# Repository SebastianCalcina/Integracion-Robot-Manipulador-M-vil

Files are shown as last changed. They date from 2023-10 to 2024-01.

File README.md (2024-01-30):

Indice del Repositorio
CódigoRobotManipulador - Esta carpeta contiene los códigos que se utilizaron para realizar las simulaciones del robot manipulador tanto en MATLAB como utilizando Python
RuedasMecanum - Archivos STL y CAD de las partes del robot móvil que se utilizaron para los análisis y también para la impresión 3D
Lista de Componentes- Lista de cada componente necesario en este proyecto.
Guía Ensamblaje- En este documento se puede observar una guía sobre el desarrollo del proyecto desde la compra de cada componente hasta el ensamblaje.

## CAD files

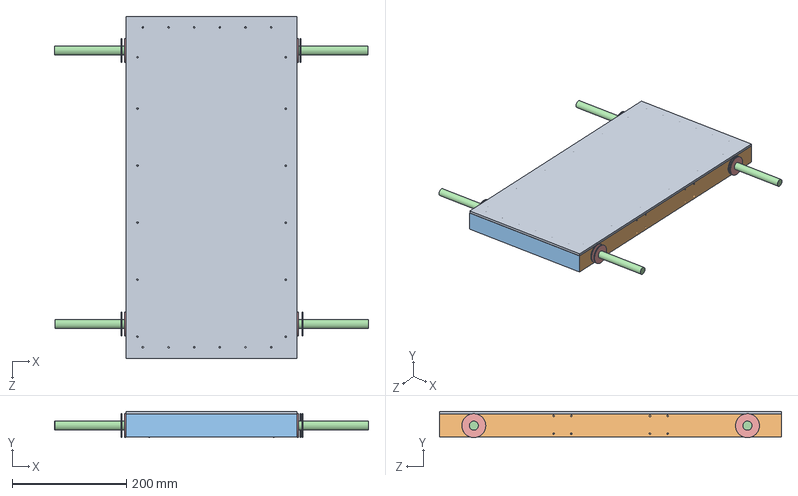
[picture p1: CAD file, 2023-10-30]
Ruedas Mecanum/files/SolidWorks/Movil armado.SLDASM
550.8 x 46.0 x 600.5 mm
Tubo Cuadrado 40x40x1mm angular x 2
tubo cuadrado 40x40x1mm angular 2 x 2
Varilla de 16mm x 2
arandela 16mm x 11
Pieza de madera

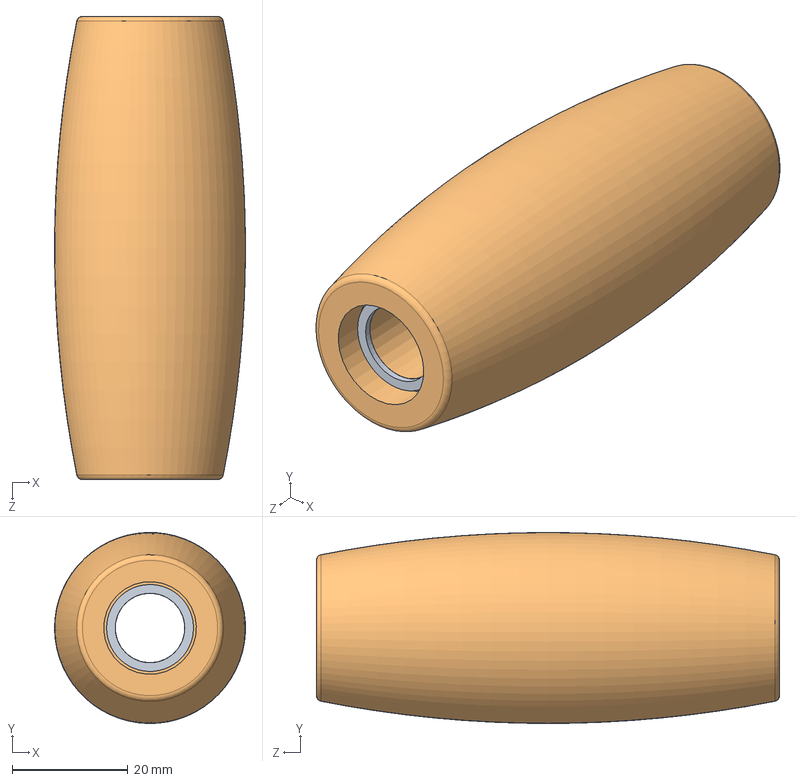
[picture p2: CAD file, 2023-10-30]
Ruedas Mecanum/files/SolidWorks/Ensamblaje Roller.SLDASM
33.0 x 33.0 x 80.0 mm
Arandela Roller x 2
Wheel_print (1)

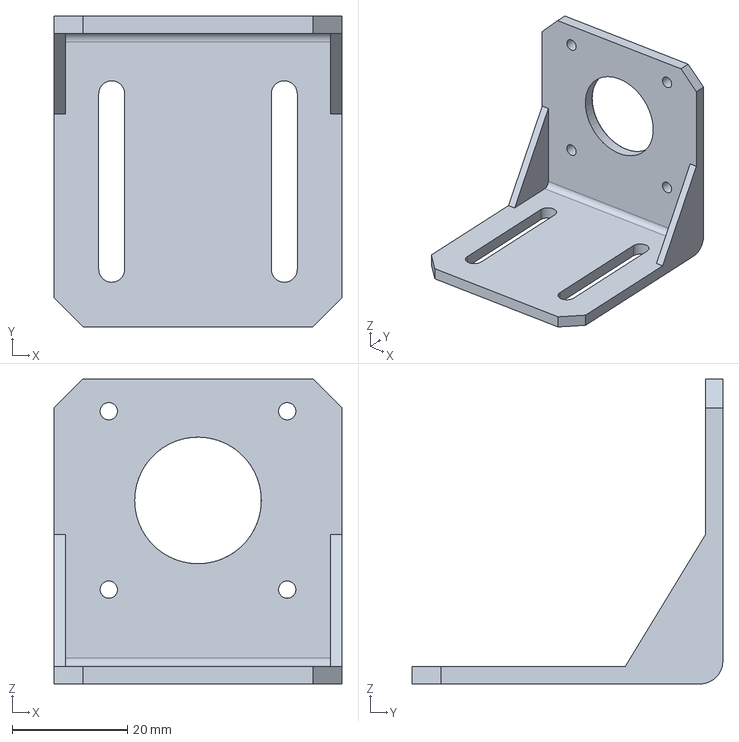
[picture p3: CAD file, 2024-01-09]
Ruedas Mecanum/files/SolidWorks/Soporte90_Nema17.stp
50.0 x 54.0 x 53.0 mm

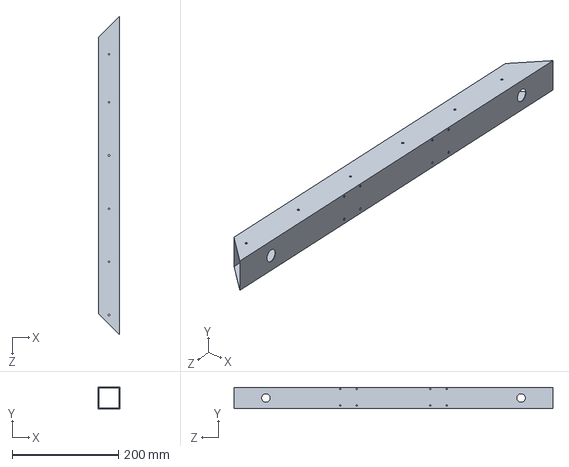
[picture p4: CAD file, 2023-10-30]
Ruedas Mecanum/files/SolidWorks/Tubo Cuadrado 40x40x1mm angular.SLDPRT
40.0 x 40.0 x 600.0 mm

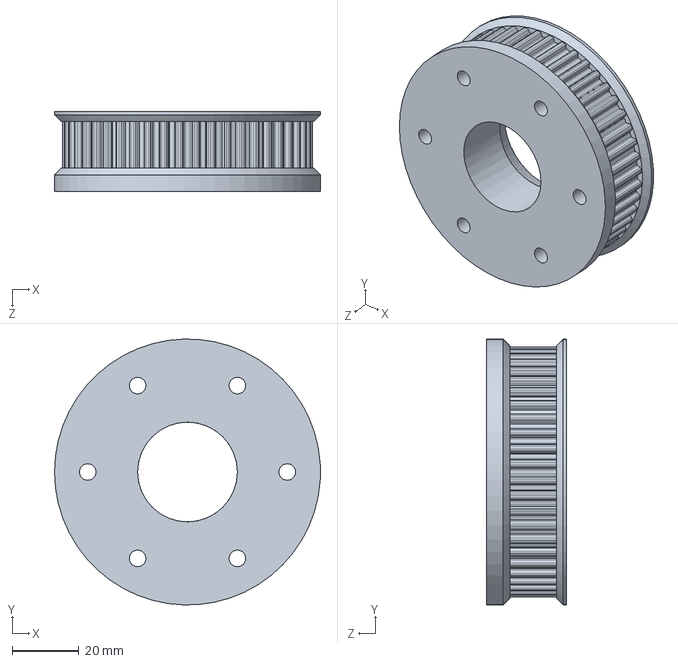
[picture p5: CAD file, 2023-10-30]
Ruedas Mecanum/files/SolidWorks/T5_48z_pulley (1).SLDPRT
80.0 x 80.0 x 24.0 mm

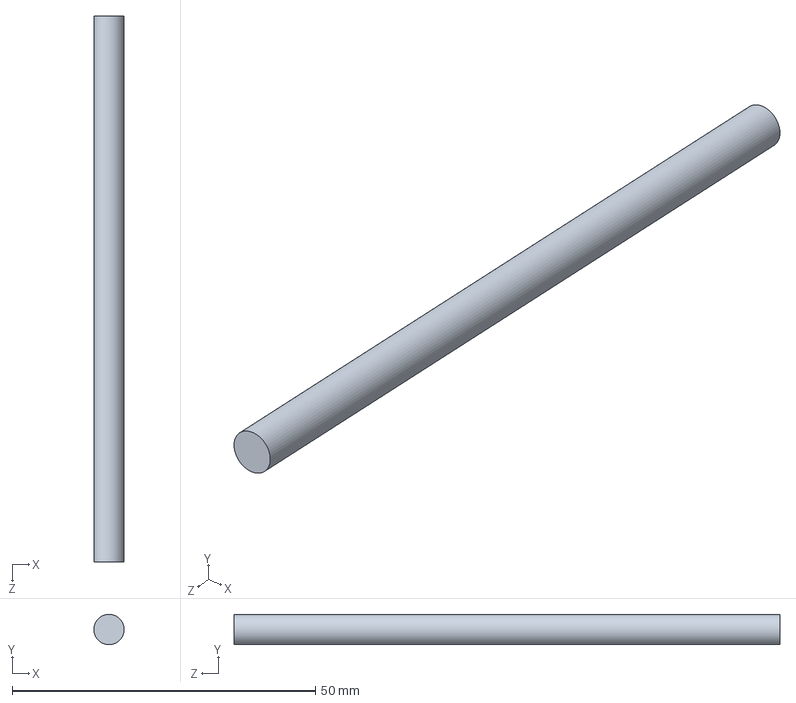
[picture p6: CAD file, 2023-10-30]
Ruedas Mecanum/files/SolidWorks/Varilla Roller 2.SLDPRT
5.00 x 5.00 x 90.0 mm

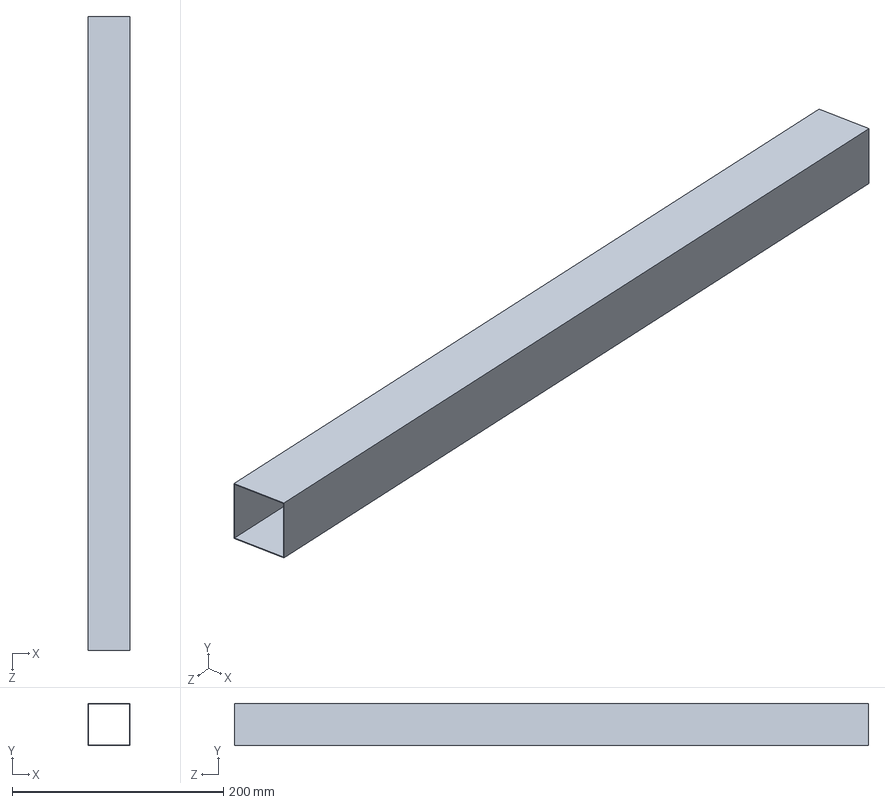
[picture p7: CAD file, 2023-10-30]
Ruedas Mecanum/files/SolidWorks/Tubo Cuadrado 40x40x1mm.SLDPRT
40.0 x 40.0 x 600.0 mm

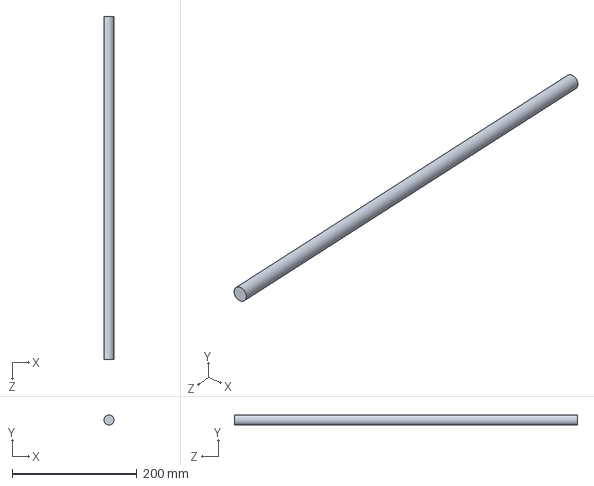
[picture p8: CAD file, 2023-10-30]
Ruedas Mecanum/files/SolidWorks/Varilla de 16mm.SLDPRT
16.0 x 16.0 x 550.0 mm

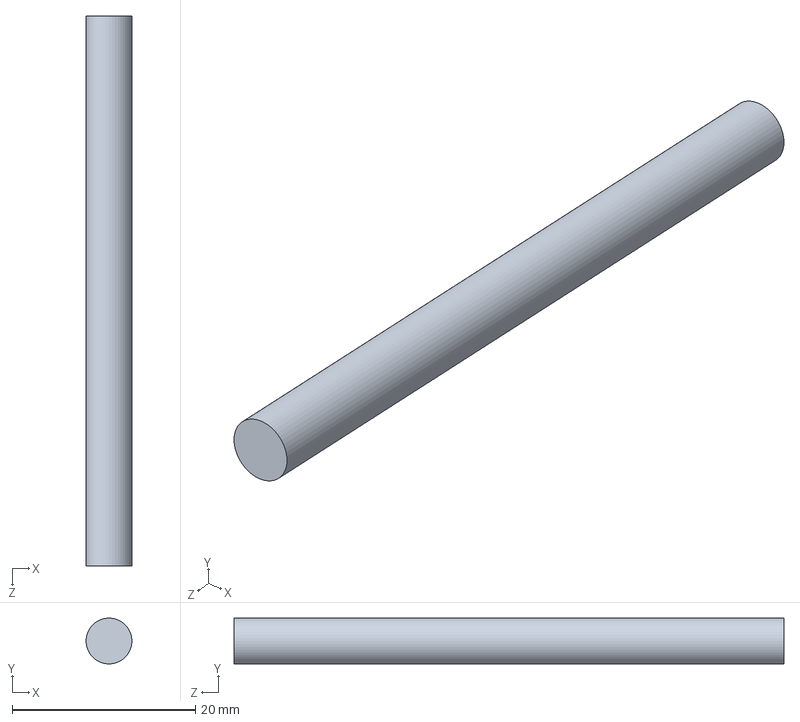
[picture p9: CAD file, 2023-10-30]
Ruedas Mecanum/files/SolidWorks/Varilla Roller 3.SLDPRT
5.00 x 5.00 x 60.0 mm

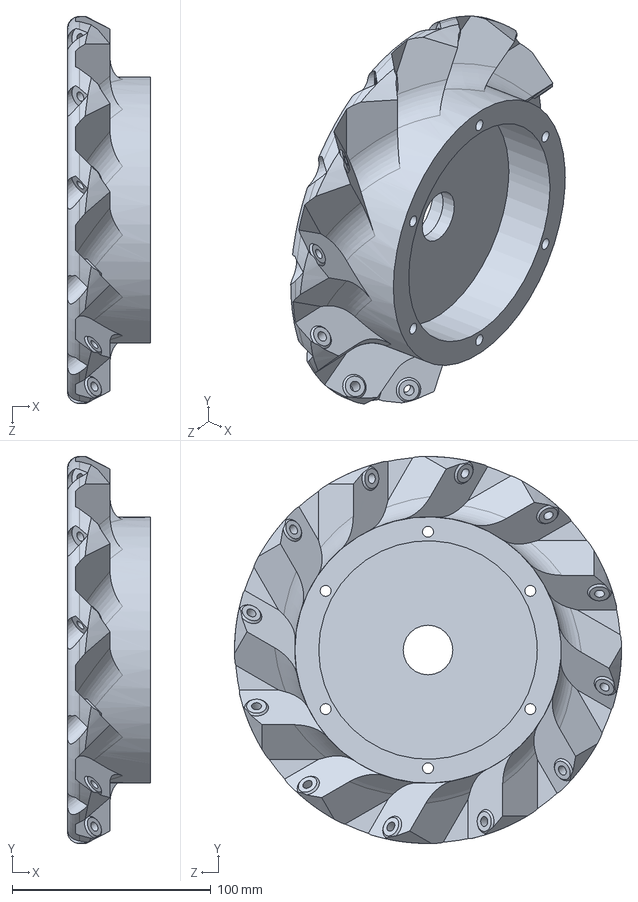
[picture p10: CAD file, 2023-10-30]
Ruedas Mecanum/files/SolidWorks/omniWheel2 (1).SLDPRT
41.8 x 194.8 x 194.8 mm

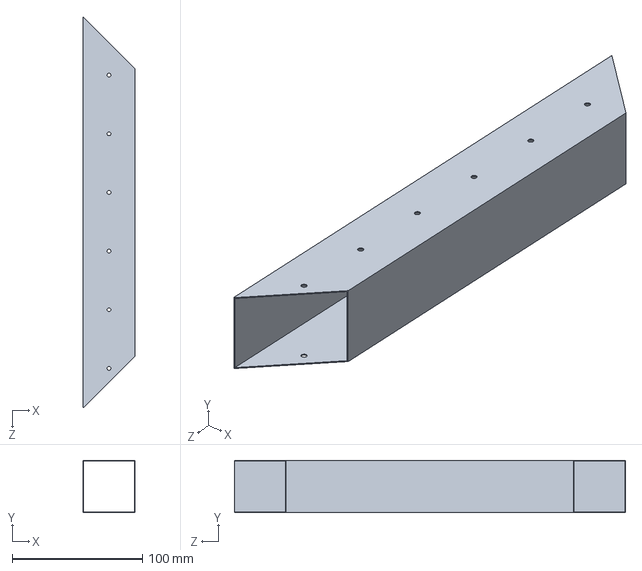
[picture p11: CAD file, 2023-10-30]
Ruedas Mecanum/files/SolidWorks/tubo cuadrado 40x40x1mm angular 2.SLDPRT
40.0 x 40.0 x 300.0 mm

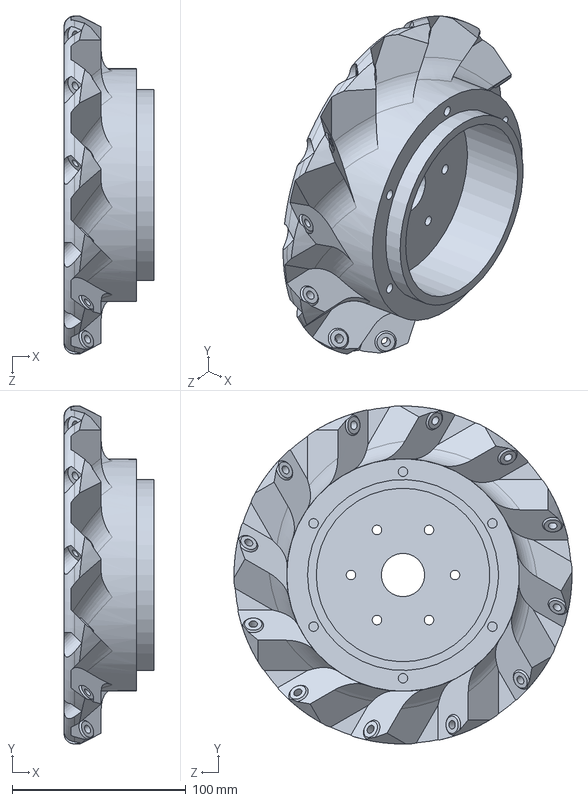
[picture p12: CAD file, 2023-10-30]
Ruedas Mecanum/files/SolidWorks/omniWheel2_B.SLDPRT
51.8 x 194.8 x 194.8 mm

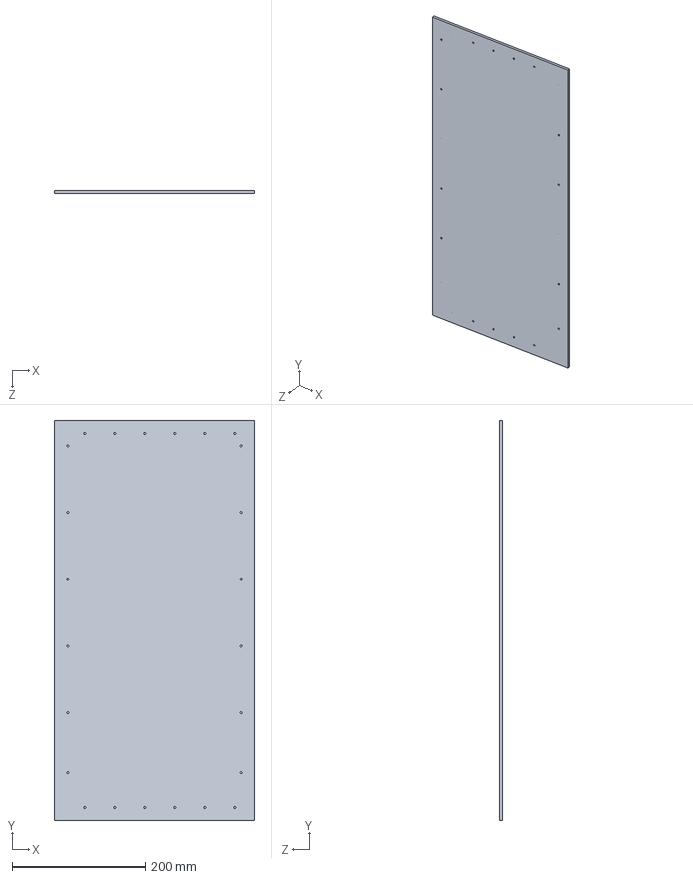
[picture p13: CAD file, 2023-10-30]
Ruedas Mecanum/files/SolidWorks/Pieza de madera.SLDPRT
300.0 x 600.0 x 5.00 mm

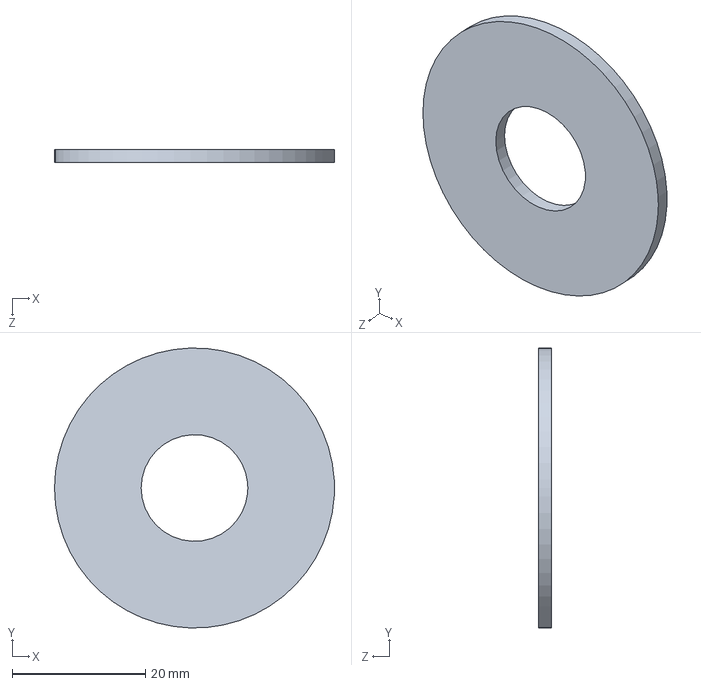
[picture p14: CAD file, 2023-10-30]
Ruedas Mecanum/files/SolidWorks/arandela 16mm.SLDPRT
42.0 x 42.0 x 2.00 mm

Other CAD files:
Ruedas Mecanum/files/SolidWorks/Wheel_print (1).SLDPRT
Ruedas Mecanum/files/SolidWorks/Arandela Roller.SLDPRT

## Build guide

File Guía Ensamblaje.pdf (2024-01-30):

Para el desarrollo del robot manipulador móvil, existen diferentes cosas que hacer, en

el cual de las más importantes están las impresiones y la selección de componentes. A

continuación, se observan los pasos para el desarrollo del proyecto.

Paso 1: Selección de herramientas

En esta sección se detallan las herramientas hardware y software utilizadas en este

proyecto. No es necesario tenerlos todos para comenzar, pero es importante tener en cuenta que

se necesitará a medida que se avance.

- Hardware
− Impresora 3D: Necesaria para imprimir el robot. Área de impresión de 300x300 mm,

suficiente para imprimir cada pieza. Si se posee una impresora con un área de impresión

de 200x200 mm, existen versiones partidas de las piezas más grandes que caben en tu

máquina.

− Estación de soldadura o cautín: Para soldar cables y componentes electrónicos a la

PCB es necesario una estación de soldadura o un cautín simplemente como se observa

en la Figura 1:

Figura 1. Estación de soldadura.

Fuente: (Amazon 2023).

## APENDICE A : GUIA DEL PROYECTO

− Multímetro: Útil a la hora de realizar conexiones electrónicas, probar sensores o

comprobar uniones soldadas. Además de que poder configurar la corriente de los

controladores de motores a la vez.

− Juego de llaves Allen y destornilladores: necesarios para asegurar los tornillos en el

conjunto del robot.

- Software

El desarrollo del robot Thor se ha realizado únicamente con herramientas de código

abierto, por lo que no es necesario gastar dinero en licencias de software.

− FreeCAD: (https://www.freecadweb.org/) Modelador paramétrico 3D. Cada pieza de Thor ha sido modelada utilizando

esta increíble herramienta. Incluso si no hay interés en el diseño de nuevas piezas o

características, se recomienda descargarlo porque hay un archivo FreeCAD que

contiene el ensamblaje del robot que te será de gran ayuda cuando se esté construyendo

el robot. El enlace de descarga es el siguiente: https://www.freecad.org/downloads.php

− KiCAD: (https://www.kicad.org/) Programa de diseño electrónico. Se utiliza para diseñar los PCB de control. Si

se presenta interés en estudiar, modificar o desarrollar electrónica para este o cualquier

otro proyecto. El enlace de descarga de este software es el siguiente:

https://www.kicad.org/download/

− Editor de código: Si es necesario profundizar en las entrañas del software o el firmware

de control, se recomienda utilizar un editor de texto con soporte de código como Atom

o también Visual Studio Code, los cuales se pueden descargar de los siguientes enlaces:

https://github.blog/2022-06-08-sunsetting-atom/

https://code.visualstudio.com/download

− Software | de | Control: | Existe | un | software | llamado | Asgard

https://github.com/AngelLM/Asgard creado especialmente para controlar a Thor.

Caso contrario se puede utilizar el firmware de GRBL al descargar la librería

directamente desde Arduino como se observa en la Figura 2, como se observa en la

siguiente Figura al buscarlo en el administrador de librerías. Dado el caso que no salga

la librería como se observa, se debe descargar la librería grbl desde el siguiente enlace

e incorporarlo dentro de la carpeta de librerías de Arduino: https://github.com/gnea/grbl

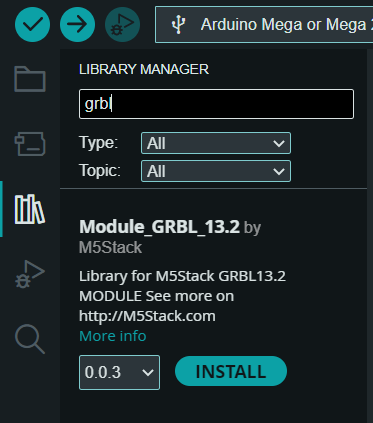
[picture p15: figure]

Figura 2. Descargar librería GRBL.

Fuente: Elaboración propia.

Paso 2: Adquisición de los materiales

Se debe buscar en diferentes tiendas los materiales descritos en el documento como

ser los pernos, tuercas, arandelas, ejes, rodamientos, etc.

Al menos en la ciudad de Santa Cruz, Bolivia existen zonas donde venden los

componentes electrónicos en toda esa zona, y venden todos los materiales de construcción en

otra zona. Los materiales de construcción se encuentran en la Av. Brasil entre 2do y 3er anillo,

como se muestra en la siguiente Figura 3.

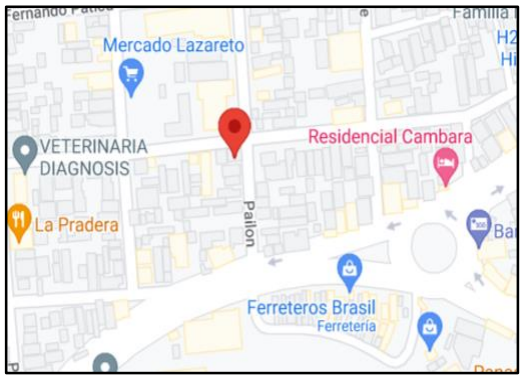
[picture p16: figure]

Figura 3. Ubicación tienda de pernos.

Fuente: Elaboración propia.

En la Tabla 1 y 2 se pueden observar los pernos y tuercas que se deben comprar

necesarios para el proyecto.

Tabla 1. Lista de pernos.

Cantidad | Diámetro [mm] | Largo [mm]
2 | M2 | 4
3 | M2 | 6
2 | M2 | 10
4 | M3 | 6
60 | M3 | 8
4 | M3 | 10
35 | M3 | 12
2 | M3 | 14
37 | M3 | 16
12 | M3 | 20
16 | M3 | 25
8 | M3 | 30
15 | M3 | 40
8 | M3 | 46
4 | M4 | 20
1 | M5 | 16

Fuente: (Larrañaga 2015).

Tabla 2. Lista de tuercas.

Cantidad | Tamaño [mm]
4 | M2
155 | M3
4 | M4
1 | M5

Fuente: (Larrañaga 2015).

Los componentes electrónicos se hallaron en el centro de la ciudad, específicamente

en la calle Charcas como se puede observar en la Figura 4, esta zona es conocida debido a que

existen gran cantidad de electrónicas en esta zona, pero para el proyecto la mayor parte de

componentes se encontraron en la tienda Sawers, Ardunel y EPY, los cuales son los 3

distribuidores más grandes de componentes electrónicos.

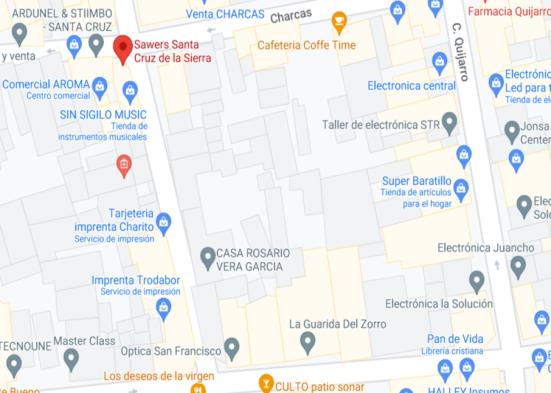
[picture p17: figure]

Figura 4. Ubicación Sawers.

Fuente: Elaboración propia.

En cualquiera de estas zonas venden herramientas, las cuales son necesarias

posteriormente para la fabricación del robot manipulador móvil. Además de que venden los

materiales necesarios para la fabricación de la placa electrónica.

Posteriormente, se muestra la tienda donde se adquirió los filamentos para la impresión

de las piezas, su ubicación se muestra en la Figura 5, cabe aclarar que en la zona de electrónicas

también se puede encontrar filamentos para impresoras 3D, pero, a un precio más alto, en este

caso se desea que sea lo más económico posible, por lo tanto, se compra los filamentos en la

tienda llamada Savin.

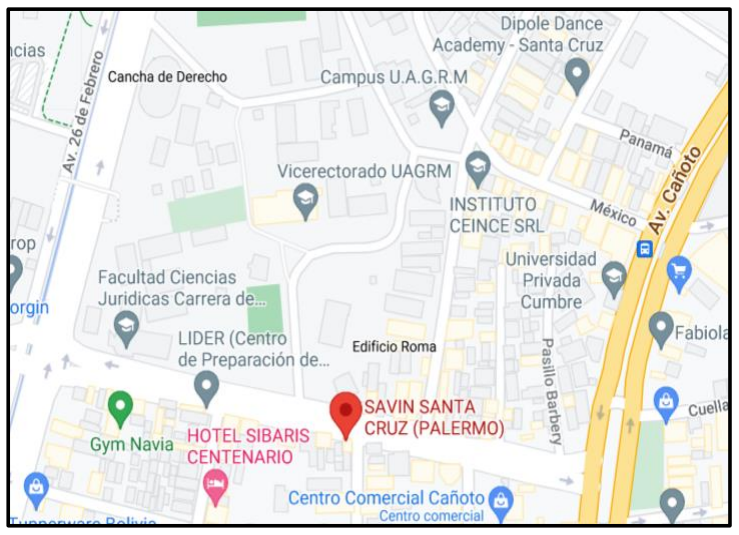
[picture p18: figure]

Figura 5. Ubicación Savin.

Fuente: Elaboración propia.

Se recomienda verificar el stock de los componentes primero mediante sus sitios web,

los cuales se adjuntan a continuación, caso contrario no exista stock en esta sucursal, se puede

solicitar desde otro departamento. En el caso de Sawers la solicitud no tiene costo y envían el

componente sin costo de envío, en el caso de Ardunel cobran el envío desde otro departamento

y uno debe recogerlo desde la Terminal Bimodal. Para el caso de Savin, existe la posibilidad de

recogerlo desde la Terminal Bimodal o desde su sucursal en el departamento de Santa Cruz,

pero tienen un costo variable.

Savin: https://www.savin.com.bo/savin3d/index.html

Sawers: https://tienda.sawers.com.bo/

Ardunel: https://tienda.sawers.com.bo/

Por último, en el caso de este proyecto, se tuvo dificultad encontrando ciertos

componentes, los cuales a continuación se muestran cuáles fueron los componentes difíciles de

encontrar, los cuales, si se encuentra una mejor solución, se recomienda aplicarla. El primer

componente son los pernos M2, en las tiendas mayoristas de pernos tampoco traen este tamaño

de perno debido a que no son pernos comerciales, son más que todo utilizados por empresas en

el ensamblaje de computadoras.

En este caso se encontró una caja en la electrónica Ardunel en la cual se encontraban

diferentes pernos de distintos tamaños entre ellos M2, M2.5, M3. Por lo tanto, se compra este

kit de pernos para poder conseguir estos pernos que sirven para el servomotor. El cual se

observa en la Figura 6.

Figura 6. Kit de pernos y tuercas.

Fuente: Elaboración propia.

El siguiente componente que no se encuentra con facilidad son los pernos M3 de 40mm

y 46mm de largo, los cuales se buscaron en diferentes tiendas pero no hubo éxito, por lo tanto,

se decidió buscar en tiendas de electronica de otros departamentos, en el cual en el siguiente

enlace se encontraron estos pernos, por lo tanto, de esta manera se solucionó la falta de stock

de este componente. Enlace: http://dro-bots.com/

Por último, el otro componente que se dificulta obtener es el motor paso a paso

17HS13-0404S-PG5, el cual no se encuentra en ninguna tienda de Bolivia, para su compra

existen dos opciones:

- Solicitar a una tienda como Sawers el pedido del motor paso a paso: En este

procedimiento existen ventajas como desventajas. La principal ventaja es que solamente cobran el costo del componente más un 5% del monto total. La desventaja es que este

procedimiento tarda alrededor de 2 a 3 meses, por lo cual, en este caso se decidió optar

por otra opción.

- Realizar la compra personalmente mediante la página oficial de motores paso a paso, en

la cual, al ser una persona que no importa componentes con frecuencia ni que tiene

conocimientos sobre ello, el precio fue alto considerando el envio y los impuestos de

los componentes. La ventaja es que solamente tarda alrededor de 15 días, por lo tanto,

se recomienda realizar el pedido mediante Sawers para evitar un costo alto. El enlace

de la página para comprar los motores paso a paso es el siguiente:

https://www.omc-stepperonline.com/nema-17-stepper-motor-bipolar-l-33mm-w-gear-

ratio-5-1-planetary-gearbox-17hs13-0404s-pg5?tracking=5c5b1e7294397 (https://www.omc-stepperonline.com/nema-17-stepper-motor-bipolar-l-33mm-w-gear-ratio-5-1-planetary-gearbox-17hs13-0404s-pg5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)

Paso 3: Impresión de los archivos CAD

Cada impresora 3D es diferente y ninguna funciona de la misma manera, sin embargo,

aquí hay algunas recomendaciones generales que pueden resultar útiles:

− Piezas Grandes: Debido a la resistencia mecánica, sería mejor imprimir las piezas

grandes (las de Articulación 2) en una sola pieza. Si no caben en la impresora, hay

versiones divididas se encuentran en la carpeta "Mods".

− Materiales: Casi todas las piezas se pueden imprimir en PLA (barato y fácil de

imprimir).

− Optodiscos: Las piezas Art1Bot, Art23Optodisk, Art4Optodisk se utilizan para bloquear

la luz de un sensor óptico en todas las posiciones excepto donde se encuentra la

ranura. Como las paredes del disco son delgadas y permite el paso de la luz, se

recomienda cubrir la superficie de estas piezas con pintura base o esmalte de uñas,

teniendo cuidado de no tapar la ranura.

− Configuración de impresión: Como las piezas son bastante grandes, se recomienda

utilizar alturas de capa gruesas, como 0,3 mm, para reducir el tiempo de impresión. En

general, 3-4 paredes deberían ser suficientes con un 20% de relleno.

− Soportes: Algunas partes de las piezas han sido diseñadas a 45 grados para evitar la

necesidad de soportes durante la impresión. Sin embargo, algunas piezas necesitan

soportes para imprimir bien, por lo que sería una buena idea habilitar los soportes para

cada ángulo superior a 50 grados en todas las impresiones.

Para iniciar la impresión de los archivos se necesita una impresora 3D con un área de

impresión de 300x300x220mm de área de impresión y boquilla de 0,4mm y adquirir la cantidad

de PLA contenido en el documento principal. Los archivos CAD se encuentra en la descripción

del | anexo | A | y | también | se | puede | descargar | en | el | siguiente | enlace:

https://github.com/AngelLM/Thor.

Se recomienda imprimir las piezas a una velocidad de 50 m/s para así obtener

resultados precisos en agujeros, engranajes, soportes, etc. Para la impresión de todos los

archivos, se utiliza el software de impresión llamado “CuraSlicer”. Este software es de acceso

gratuito, por lo tanto, no existe problema en su adquisición.

En la Figura 7 se observa la configuración que se debe realizar para la impresión de

las piezas y así tener un buen acabado y tener los menores errores posibles en su impresión. En

esta Figura se observa la configuración de la sección de calidad, en el cual se modifica la altura

de capa, la altura de capa inicial y el ancho de línea, estos parámetros se cambian debido a que

por defecto vienen en unos valores diferentes, pero con estos parámetros se puede ahorrar un

poco de tiempo en la impresión sin afectar en la calidad de la pieza.

Figura 7. Sección de Calidad en CuraSlicer.

Fuente: Elaboración propia.

La siguiente configuración que se debe cambiar son la cantidad de capas superiores e

inferiores, las cuales se pueden aumentar o disminuir, pero es importante mantenerlas en 3 para

así tener un buen acabado y a la vez que no tome mucho tiempo extra de impresión como se

observa en la Figura 8.

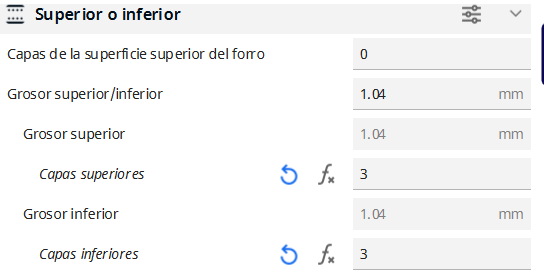
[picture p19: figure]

Figura 8. Sección de Superior o inferior en CuraSlicer.

Fuente: Elaboración propia.

En la Figura 9 se observa la sección de relleno, la cual se coloca como densidad de

relleno de 30% y se utiliza el patrón de relleno cúbico, este relleno cúbico tiene la característica

de que es un relleno que hace que la estructura de la pieza sea estable y también a un tiempo

moderado, existen otros rellenos los cuales tardan más tiempo y tienen mayor durabilidad, pero

con las características que proporciona este relleno es suficiente.

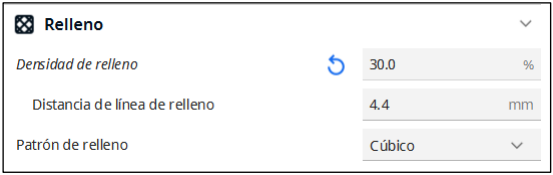
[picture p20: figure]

Figura 9. Sección de Relleno en CuraSlicer.

Fuente: Elaboración propia.

Un consejo útil es emplear laca para el cabello en piezas grandes. Esto se debe a que,

en ausencia de una impresora 3D con ambiente cerrado, cualquier corriente de aire a una

temperatura distinta de la que se encuentra la cama de impresión puede dar lugar al fenómeno

conocido como "warping". El warping se refiere al levantamiento de las esquinas de la pieza en

proceso de impresión, y es un error bastante común en la impresión 3D.

Otro consejo previamente a realizar la impresión es realizar la calibración de la

impresora 3D, principalmente las excéntricas, los pasos/mm de los motores paso a paso y por

último, los resortes que nivelan las cuatros esquinas de la cama de la impresora 3D.

A continuación, se presentan los pasos para verificar el estado de las excéntricas:

1. Asegúrate de que las excéntricas pueden moverse fácilmente al ejercer una ligera

presión con el dedo.

2. Verifica que, si las excéntricas se mueven con facilidad, pero no provocan el giro

del extrusor o la cama, esto indica que están demasiado flojas.

3. Si las excéntricas no se mueven y presentan signos de desgaste, es necesario

aflojarlas.

Realizar estos pasos se garantiza el correcto funcionamiento de las excéntricas en tu

impresora 3D, las cuales se muestran a continuación.

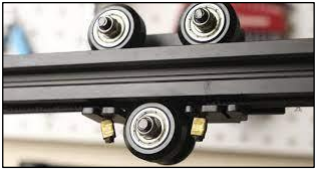
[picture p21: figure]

Figura 10. Excéntricas en una impresora 3D.

Fuente: Elaboración propia.

Los resortes de la cama desempeñan un papel crucial al nivelar la superficie de

impresión en una impresora 3D. Esto es de suma importancia para evitar daños en la cama y

garantizar una impresión precisa. Aunque muchas impresoras 3D modernas están equipadas

con sistemas de nivelación automática que utilizan sensores táctiles, se aconseja realizar un

nivelado manual utilizando una hoja de papel A4, como se ilustra en la Figura 11, esto se debe

realizar en cada una de las cuatro esquinas de la cama y por último en el centro, para así

modificar el valor de z offset.

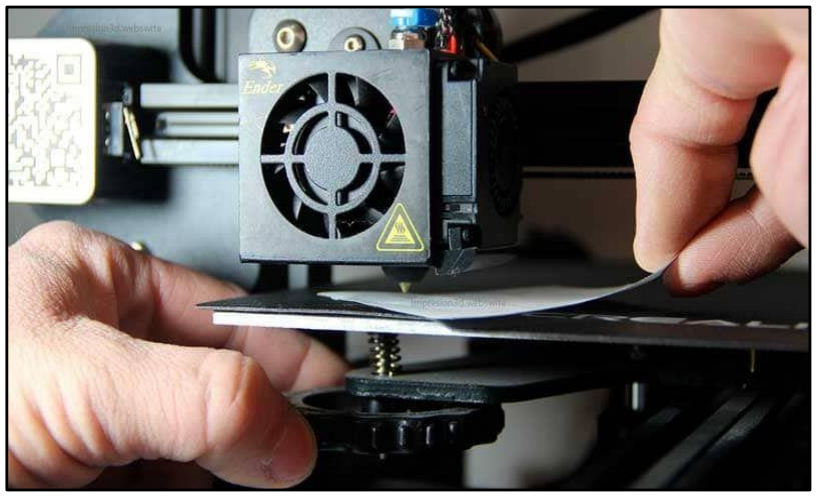
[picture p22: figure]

Figura 11. Calibración de una impresora 3D.

Fuente: Elaboración propia.

Por último, en la Tabla 3 se pueden observar las piezas a imprimir con su respectivo

tiempo de impresión.

Tabla 3. Partes del Brazo manipulador de 6 grados de libertad “Thor”.

Pieza | Tiempo de impresión | Consumo de filamento
Pieza 1: BaseBot | 19 horas | 261 gramos
Pieza 2: BaseTop | 7 horas y 26 minutos | 129 gramos
Pieza 3: BaseBearingFix | 2 horas y 5 minutos | 35 gramos
Pieza 4: BaseBoxBody | 23 horas y 9 minutos | 289 gramos
Pieza 5: BaseBoxCover | 5 horas y 9 minutos | 93 gramos
Pieza 6: Art1Body | 1 día y 7 horas. | 421 gramos
Pieza 7: Art1Bot | 5 horas y 42 minutos. | 75 gramos
Pieza 8: Art1Top | 8 horas y 22 minutos | 132 gramos
Pieza 9 y 10: Art1FanHolder | 30 minutos | 4 gramos
Pieza 11: Art1GearMotor | 36 minutos | 7 gramos
Pieza 12: Art1OptoFix | 20 minutos | 4 gramos
Pieza 13: Art2BodyA | 12 horas y 13 minutos | 168 gramos
Pieza 14: Art2BodyACover1 | 2 horas | 33 gramos
Pieza 15: Art2BodyACover2 | 2 horas | 31 gramos
Pieza 16: Art2BodyAWindow | 2 horas | 27 gramos
Pieza 17: Art2BodyB | 13 horas y 26 minutos | 198 gramos
Pieza 18: Art2BodyBCover | 3 horas y 53 minutos | 66 gramos
Pieza 19: Art2BodyUnion | 4 horas y 40 minutos | 60 gramos
Pieza 20: Art2GearMotor | 1 hora y 22 minutos | 14 gramos
Pieza 21 y 22: Art2SideCover | 6 horas y 49 minutos | 103 gramos
Pieza 23: Art3Body | 1 dia y 1 hora | 341 gramos
Pieza 24: Art3Pulley | 3 horas y 3 minutos | 37 gramos
Pieza 25: Art3TensionerBody | 16 minutos | 2 gramos
Pieza 26: Art3TensionerPulley | 16 minutos | 3 gramos
Pieza 27: Art4Body | 23 horas y 30 minutos | 307 gramos
Pieza 28: Art4BearingFix | 10 minutos | 2 gramos
Pieza 29: Art4BearingPlug | 4 minutos | 1 gramo
Pieza 30: Art4BearingRing | 2 horas | 24 gramos
Pieza 31: Art4BodyBot | 2 horas y 18 minutos | 32 gramos
Pieza 32: Art4BodyFan | 3 horas | 35 gramos
Pieza 33: Art4MotorFix | 22 minutos | 4 gramos
Pieza 34: Art4MotorGear | 35 minutos | 7 gramos
Pieza 35: Art4OptoDisk | 34 minutos | 8 gramos
Pieza 36: Art4TransmissionColumn | 4 horas y 35 minutos | 59 gramos
Pieza 37: Art23OptoDisk | 24 minutos | 4 gramos
Pieza 38: Art56GearPlate | 5 horas y 12 minutos | 67 gramos
Pieza 39: Art56MotorCoverRing | 2 horas y 24 minutos | 34 gramos
Pieza 40: Art56MotorHolderA | 35 minutos | 6 gramos
Pieza 41: Art56MotorHolderB | 34 minutos | 6 gramos
Pieza 42: Art56SmallGear | 1 hora y 39 minutos | 15 gramos
Pieza 43: CommonBearingFix | 23 minutos | 4 gramos

Pieza 44: CommonBearingFixThrough | 23 minutos | 3 gramos
Pieza 45: GripperActiveArm | 18 minutos | 9 gramos
Pieza 46: GripperArm | 9 minutos | 2 gramos
Pieza 47: GripperBot | 2 horas y 17 minutos | 25 gramos
Pieza 48: GripperFinger | 1 hora y 30 minutos | 20 gramos
Pieza 49: GripperPassiveArm | 15 minutos | 3 gramos
Pieza 50: GripperTop | 1 hora y 9 minutos | 16 gramos

Fuente: Elaboración propia.

Paso 3: Elaboración de la placa PCB

Dentro de la fabricación de la PCB, existen diferentes pasos a realizar, el cual el

primero es determinar los requerimientos y los componentes que conforman esta placa

electrónica, lo cual se realiza en el documento, pero para realizar esto se necesita un software

de electrónica, en este caso se utiliza el software llamado Proteus, el cual permite realizar

diseños esquemáticos y también realizar diseños para la fabricación de placas electrónicas.

En el documento se muestra un diseño en 3D de la placa electrónica, el cual se realiza

mediante la descarga de los archivos “STEP” de los componentes electrónicos. Estos archivos

se encuentran normalmente en la página snapEDA, la cual contiene muchos archivos CAD de

los componentes electrónicos mayormente utilizados.

Estos archivos se deben colocar en la carpeta que se cree el archivo del proyecto, para

que así automáticamente se coloquen, caso contrario se pueden exportar estos archivos uno por

uno al programa, pero esto es más tardío.

En algunos casos se realiza primero el diseño esquemático, pero en este caso se realiza

directamente el diseño en la sección PCB del software, debido a que cuando se realiza el diseño

esquemático primero y se lo trata de exportar, las conexiones que realiza el software

automáticamente suelen no estar correctamente hechas, por lo tanto, para ahorrar tiempo se

procura realizarlo directamente.

El proceso de diseñar y fabricar una placa de circuito impreso (PCB) implica varios

pasos. A continuación, se detallan los pasos para llevar a cabo este proceso:

### 1. Diseño del Esquemático:

Definir la funcionalidad del circuito y crear un esquema eléctrico en software de diseño

como KiCad, Eagle, Altium, Proteus, etc.

En este caso se utiliza Proteus para realizar el diseño electrónico, por lo tanto, una vez

se tiene eso definido, se procura a definir la funcionalidad del circuito.

En el proyecto Thor, se parte de un circuito base que incluye motores paso a paso como

componentes principales encargados de controlar el movimiento y la posición del brazo

manipulador. Para determinar qué motores son adecuados para el robot móvil, cuyo objetivo es

conocer su posición en los ejes x, y, se opta por utilizar motores paso a paso. Estos motores

permiten obtener información precisa sobre la posición y velocidad del robot móvil a través de

los pasos dados.

Una vez definidos los motores a utilizar, se identifica la necesidad de contar con

controladores específicos para los motores paso a paso. Con el propósito de lograr una alta

precisión en el robot manipulador, se elige el controlador DRV8825. Por otro lado, para el robot

móvil, donde no se requiere la misma precisión, se emplea el controlador A4988. Esta selección

de controladores se basa en la necesidad de adaptar la precisión de control a las características

particulares de cada componente del proyecto.

El uso de finales de carrera no se cambia ni tampoco el final de carrera a utilizar, por

lo tanto, ese componente se mantiene de la misma manera, así como los ventiladores y el

servomotor MG995.

Por último, se considera la posibilidad de colocar la computadora encima del robot

móvil para realizar el control del robot móvil, pero se la descarta debido a distintos factores:

- Seguridad: El colocar una computadora encima del robot móvil puede salir mal

si es que no se tiene cuidado en las velocidades utilizadas o en los movimientos

del brazo manipulador.

- Espacio: No hay el suficiente espacio para colocar una computadora encima

del robot móvil y no es la opción más eficiente.

Debido a estas consideraciones se decide implementar un módulo Bluetooth, para así

poder mandar los comandos a distancia, además de que no se pretende que se emplee en un área

grande, por lo tanto, con el alcance del Bluetooth es más que suficiente.

### 2. Diseño de la PCB

- Abrir un nuevo proyecto de PCB en Proteus.
- Establecer una medida de la placa según el espacio que se pueda utilizar para

así tener una mejor distribución de los componentes.

- Coloca los componentes en la PCB y enruta las conexiones entre ellos.
- Revisar que no existan rutas en 90 grados para así evitar cortos circuitos.
- Revisar varias veces si todas las GND están conectadas entre ellas.
- Asegurarse de que el diseño sea eficiente y tenga rutas de señal cortas para

minimizar interferencias electromagnéticas.

- Considera la disposición de componentes para facilitar el ensamblaje.}
- Realiza comprobaciones de reglas de diseño para asegurarte de que no haya

errores, como cortocircuitos o violaciones de restricciones.

### 3. Generación de Archivos:

Exportar el archivo PDF desde Proteus. Estos archivos describen la capa de cobre,

capas de máscara, capas de soldadura, taladros, etc. La cual es importante para realizar la

fabricación PCB.

Para la fabricación PCB existen dos opciones:

- Enviar el diseño a que sea realizado mediante CNC, lo cual es una manera más

sencilla de realizar la placa PCB, pero tiene un costo mayor.

- Realizarlo en el aula o en casa, para así tener aprender distintos conceptos de

la electrónica y habilidades de soldadura.

Dado el caso que se elija realizar la placa por cuenta propia, se debe comprar los

componentes necesarios, los cuales se adjuntan a continuación en la Tabla 4:

Tabla 4. Lista de componentes para la placa.

Componente | Cantidad
Resistencia 220 | 5
Resistencia 1k | 5
Regulador de voltaje | 1
Fusible GF1100 | 1
Controlador A4988 | 4
Controlador DRV8825 | 7
Arduino Mega 2560 | 1
Espadines Hembra | 20
Espadines Macho | 20
Bluetooth HC-05 | 1
Placa de cobre 15x15cm | 1
Metro de estaño | 4
Cautín | 1
Pasta de soldar | 1
Esponja de acero | 1
Estilete | 1
Litro de ácido férrico | 1

Fuente: Elaboración propia.

Una vez se tienen los componentes necesarios, se procede a realizar la placa PCB, el

primer paso es tener la hoja impresa en papel termotransferible como se observa a continuación

en la Figura 12:

Figura 12. Hoja impresa en papel termotransferible.

Fuente: Elaboración propia.

Una vez se corta los papeles a la medida de la placa, se la debe colocar justo a la

medida sin que sobresalga, esto es importante ya que puede arruinar el diseño desde un

principio. Posterior a esto, se le debe pasar con una esponja de acero inoxidable a la plancha

para sacar cualquier impureza y luego con una plancha caliente para que el contenido de la hoja

pase a la placa de cobre. Este paso se puede observar en la Figura 13 mostrada a continuación.

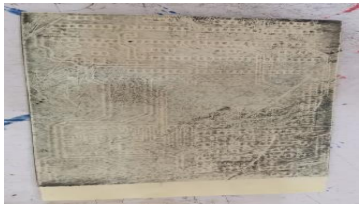
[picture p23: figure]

Figura 13. Hoja planchada en la placa de cobre.

Fuente: Elaboración propia.

Este paso se realiza tanto para la cara superior como para la cara inferior, por lo tanto,

una vez se realiza esto, se lo debe retirar para que así quede como se ilustra en la Figura 14:

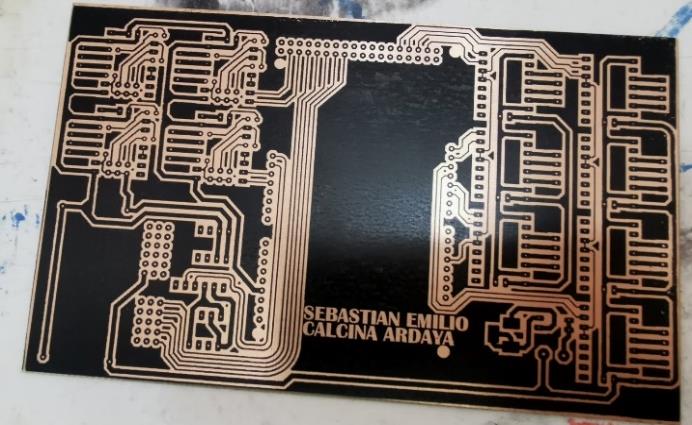
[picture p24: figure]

Figura 14. Diseño PCB transferido a la placa de cobre.

Fuente: Elaboración propia.

Una vez que se tiene el circuito planchado en la placa, se debe asegurar que el diseño

no se salga utilizando ácido férrico, en el cual se diluye en un litro de agua un poco del ácido

férrico para así realizar el grabado utilizando esta mezcla como se observa en la Figura 15.

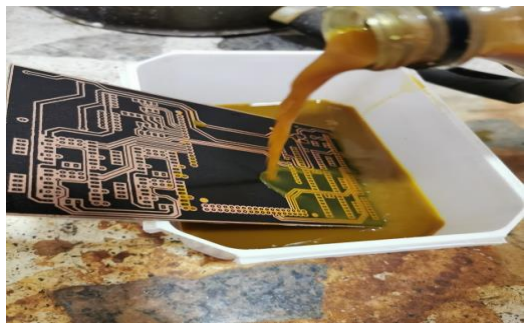
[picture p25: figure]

Figura 15. Grabado del diseño PCB.

Fuente: Elaboración propia.

Este paso se debe repetir una y otra vez hasta que se vea que la placa tiene un color

resplandeciente y posterior a ello, se le debe pasar nuevamente con una esponja de acero para

eliminar los espacios negros que existen en la placa PCB, de manera que queda como se observa

en la Figura 16.

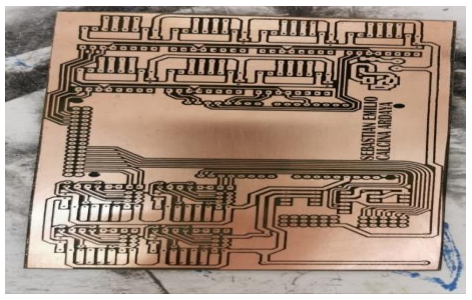
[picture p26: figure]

Figura 16. Grabado del diseño PCB.

Fuente: Elaboración propia.

Como se observa en la anterior Figura quedan los residuos alrededor, por lo tanto, se

debe tener un espacio de trabajo que se pueda ensuciar, o utilizar una manta por debajo para así

no ensuciar el espacio de trabajo.

Posterior a ello, se deben realizar los agujeros para colocar los espadines necesarios

para conectar los componentes posteriormente, en la Figura 17 se observa cómo están los

agujeros realizados, los cuales tienen distintas medidas, pero la mayor parte son de 0.1 mm y el

agujero más grande es de 3mm, los cuales son para poder asegurar la placa electrónica en la

caja de componentes.

Figura 17. Agujeros en la placa PCB.

Fuente: Elaboración propia.

Una vez se realizan los agujeros, el siguiente paso es realizar la soldadura de los

componentes como se observa a continuación en la Figura 18, en este paso se debe realizar con

mucha paciencia las soldaduras y asegurar de que no se conecten entre pines debido a que puede

causar un corto circuito cuando se realice alguna conexión.

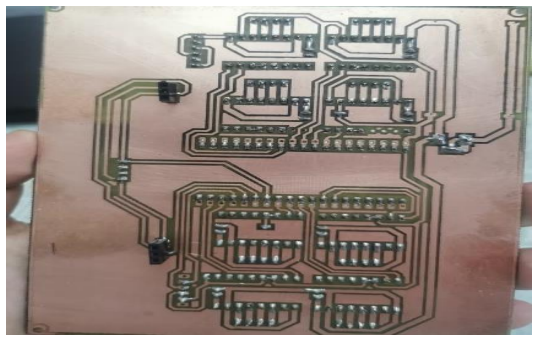
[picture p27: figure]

Figura 18. Soldadura en la placa PCB.

Fuente: Elaboración propia.

Una vez se terminan las soldaduras, se observa que la placa queda de la siguiente

manera que se observa en la Figura 19, la cual ya está lista para realizarse las pruebas

correspondientes de cada uno de los componentes, pero es recomendable verificar la

continuidad utilizando un tester.

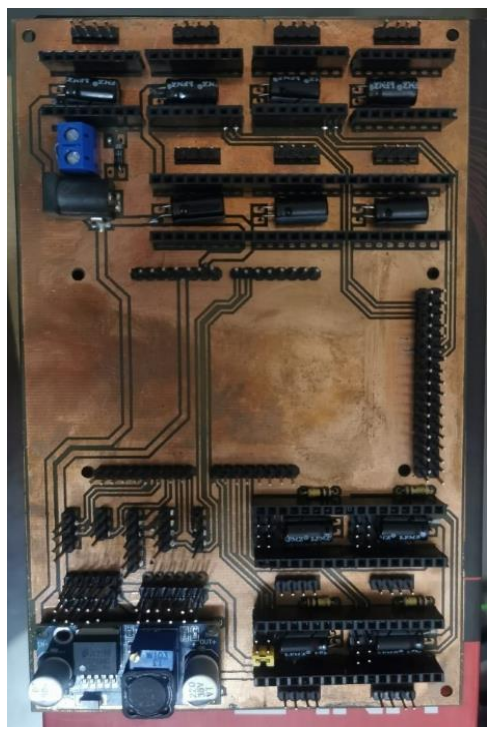
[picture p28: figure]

Figura 19. Placa PCB terminada.

Fuente: Elaboración propia.

Paso 4: Ensamblaje físico del Robot Manipulador móvil

El ensamblaje del robot manipulador móvil se detalla a continuación, el cual se

recomienda realizar el proceso de ensamblaje desde la última articulación hasta abajo, para así

llevar los cables de los componentes electrónicos desde la última articulación hasta la base, el

cual es el espacio donde se encuentra la placa electrónica.

He de aclarar que también existen diferentes maneras de verificar como se realiza el

ensamblaje, en el canal de “Sr. Ferrete” se encuentra el ensamblaje en su mayor parte del robot

manipulador Thor y además el autor de este proporciona el archivo CAD donde se encuentra el

ensamblaje y una simulación que realiza paso a paso el ensamblaje del robot, donde menciona

que pieza y cuanta cantidad de pernos y tuercas se necesita en ese paso. (http://thor.angel-

lm.com/documentation/assembly/)

Garra o Gripper

El primer paso es colocar las tuercas correspondientes en cada espacio que tiene forma

de tuerca o forma hexagonal como se puede observar en la siguiente Figura que corresponde a

la pieza Art56MotorCoverRing. Además de que el ensamblaje se puede encontrar a detalle en

el siguiente enlace: https://www.youtube.com/watch?v=_8irjosCVqg&ab_channel=AngelLM

Figura 20. Forma hexagonal de las tuercas.

Fuente: Elaboración propia.

En este caso, se tuvo dificultad al colocar las tuercas a presión, por lo tanto, se

recomienda utilizar aire caliente para así ablandar la pieza y que, entre correctamente la tuerca,

también existe el caso en que el espacio donde entra la tuerca es más grande que la tuerca, para

este caso se debe utilizar pegamento para así evitar que las tuercas se caigan cuando se comienza

a colocar los pernos. Para este caso se utilizó una secadora de pelo y el pegamento “La gotita”,

pero también se puede utilizar la hornilla de la cocina para calentar la pieza. Para esta pieza que

se muestra a continuación se necesita en total:

- 10 tuercas M3
- 5 pernos M3x12mm
- 4 pernos M3x20mm
- 4 pernos M3x16mm

Entonces como se menciona anteriormente el primer paso es colocar las tuercas y

colocar el servomotor MG995 como se observa en la Figura 21.

Figura 21. Primer paso del ensamblaje del Gripper.

Fuente: Elaboración propia.

El siguiente paso es colocar las piezas GripperActiveArm y GripperPassiveArm, las

cuales deben coincidir, es decir, que sus puntas estén orientadas en el mismo ángulo, para así

cuando se coloque las piezas GripperFinger, no exista errores.

Figura 22. Segundo paso del ensamblaje del Gripper.

Fuente: Elaboración propia.

Una vez se colocan estas piezas, se debe colocar las piezas GripperFinger que se debe

tener especial cuidado para que coincidan como se colocan en la siguiente Figura, deben quedar

alineadas las piezas que agarran a los objetos.

Figura 22. Último paso del ensamblaje del Gripper.

Fuente: Elaboración propia.

Cuarta y quinta articulación

Para el ensamblaje de estas dos articulaciones que conectan a la garra se necesitan

distintos materiales, los cuales se describen a continuación.

- 1 Tuerca M5
- 1 M5x18mm
- 37 tuercas M3
- 4 625ZZ Rodamiento
- 18 M3x8mm
- 2 M3x6mm
- 12 M3x28mm
- 12 M3x16mm
- 4 M3x12mm
- 2 M2x10mm
- 2 M2x6mm
- 4 tuerca M2
- 30 bolillas de 6mm
- 1 varilla de 102x5mm
- 2 poleas GT2 de 40 dientes
- 2 correa GT2x208mm
- 2 poleas GT2 de 20 dientes
- 2 ventiladores 40x40mm

Entonces una vez que se tienen todos estos materiales en la mesa, como se menciona

anteriormente se deben colocar todas las tuercas para así ahorrar tiempo, ya que en su mayoría

todas las tuercas se deben introducir con la ayuda de una secadora o pistola de calor.

En la Figura 23 se muestra lo que debe realizarse dentro del cuerpo de la articulación

4, esto se muestra así previamente porque cuando el ensamblaje de estas piezas no se ve

claramente dentro, como se puede ver están las piezas Art56CoverMotorRing, Art56SmallGear

y la pieza Art56GearPlate y dos poleas de 40 dientes, en esta pieza se debe tener especial

cuidado debido a que si se atornilla mucho el perno M5, los dientes de la pieza Art56SmalGear

no encajan con los dientes de la otra pieza. Además de que como se menciona en el documento,

las poleas de 40 dientes varían según el fabricante, en este caso el diámetro varia y no encaja

en la pieza, por lo tanto, se realiza una modificación, pero también existe la posibilidad de

rellenarlo para que la polea encaje, se hizo la prueba de rellenarlo con cierta parte de una correa

para que así encaje y se pueda utilizar.

Figura 23. Primer paso del ensamblaje de la Articulación 5 y 6.

Fuente: Elaboración propia.

Además de que se debe tener en cuenta que no se debe olvidar de colocar las correas

antes de colocar los otros componentes electrónicos, como se puede observar en la Figura 24.

Figura 24. Segundo paso del ensamblaje de la Articulación 5 y 6.

Fuente: Elaboración propia.

En esta pieza de la articulación 4, hay una varilla que va atravesada la cual conecta

ambas poleas y como se puede ver a un lado derecho, está el final de carrera switch. Luego de

esto, se debe colocar los 2 motores que van a ir conectados mediante poleas, para que estos

mediante las correas ejerzan el movimiento de esta articulación, cada motor cuenta con 2 piezas que va conectado en la parte superior e inferior del motor, las cuales funcionan como un carril

en la articulación 4, en la Figura 25 se puede observar cómo van estas 2 piezas con el motor.

Figura 25. Tercer paso del ensamblaje de la Articulación 5 y 6.

Fuente: Elaboración propia.

Una vez se colocan los 2 motores y se coloca la correa, el siguiente paso es cerrar el

cuerpo de esta articulación para que se pueda colocar las otras piezas que conectan con la

articulación 3. Esto se puede observar en la siguiente Figura, lo cual es importante sacar todos

los cables con el debido cuidado para así no arruinar los conectores.

Figura 26. Cuarto paso del ensamblaje de la Articulación 5 y 6.

Fuente: Elaboración propia.

Una vez se sacan los cables desde la garra hasta la articulación 4 y 5, se los debe hacer

pasar por el agujero de la articulación 3 y colocar la pieza que realiza el movimiento de esta

articulación como se observa en la siguiente Figura.

Figura 27. Último paso del ensamblaje de la Articulación 5 y 6.

Fuente: Elaboración propia.

Tercera articulación

En la tercera articulación no existen problemas o especiales cuidados en su ensamblaje,

de hecho, es una de las piezas que se ensambla sin dificultad. Como se menciona anteriormente,

el primer paso es colocar todas las tuercas antes de realizar cualquier otra cosa, para así ahorrar

tiempo en el armado.

Luego de este paso se debe colocar el ventilador, como se puede observar en la Figura

28, este ventilador tiene unas dimensiones de 40x40x10mm.

Figura 28. Primer paso del ensamblaje de la Articulación 3.

Fuente: Elaboración propia.

Una vez que se instala el ventilador, es fundamental prestar atención al cableado,

asegurándose de que este se extienda hasta la caja que alberga todos los componentes

electrónicos. Posteriormente, se procede a la colocación del motor paso a paso. Para ello, se

acopla un engranaje al eje del motor, permitiendo su conexión con la articulación 4 del sistema.

El siguiente paso implica la fijación de la correa en la pieza denominada Art3Pulley.

La tensión de esta correa se ajusta cuidadosamente mediante el perno correspondiente, como se

muestra en la Figura 29.

Figura 29. Segundo paso del ensamblaje de la Articulación 3.

Fuente: Elaboración propia.

En la Figura 30 se observa como los cables se los va bajando desde la parte superior

del robot manipulador hasta la articulación 3. Se debe tener cuidado y antes de seguir, se

recomienda colocar nombre a los cables de los componentes para que, al realizar las conexiones

a la placa, no se malgaste tiempo viendo cual cable corresponde a cada componente.

Figura 30. Último paso del ensamblaje de la Articulación 3.

Fuente: Elaboración propia.

Segunda articulación

En esta articulación se tienen distintas piezas, las cuales en su mayoría se acoplan a

presión. En estas dos piezas se colocan dos rodamientos los cuales funcionarán para los ejes

que se colocan para conectar tanto con la articulación 1 como con la articulación 3, esto se

observa en la Figura 31.

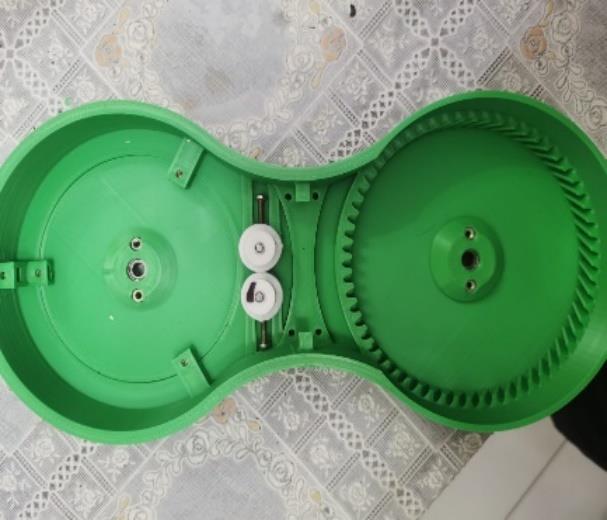
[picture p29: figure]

Figura 31. Ensamblaje de la Articulación 2.

Fuente: Elaboración propia.

Una vez se colocas las piezas correspondientes en esta pieza, se deben colocar los

finales de carrera en la contraparte, para que de esa manera quede unido.

Primera articulación

La primera articulación es la articulación más importante, esto debido a que en esta se

encuentran los motores con reducción planetaria. Luego de pasar todos los cables por todas las

articulaciones previas, se debe ensamblar la primera articulación, la cual es la más sencilla en

ensamblaje, a excepción de cuando se pasan los cables para ir a la base, una vez se colocan los

motores y se pasan los motores quedan de la siguiente manera junto a cada una de los engranajes

y polea correspondientes para cada motor.

Se recomienda tener especial cuidado al colocar los motores debido a que la parte

frontal de la pieza tiene partes delgadas, las cuales tienden a romperse debido a su grosor.

Figura 32. Ensamblaje de la Articulación 1.

Fuente: Elaboración propia.

Base

Esta pieza es relativamente sencilla también debido a que el primer paso es colocar el

final de carrera y el ventilador de esta pieza como se observa a continuación.

Figura 33. Primer paso del ensamblaje de la base.

Fuente: Elaboración propia.

Luego de realizar esto, se debe colocar el motor en el lugar que se ve en la anterior

imagen, la cual se le debe colocar un engranaje acoplado a su eje, además de que esta pieza

incluye un rodamiento el cual se ve acoplado en la Figura 34, este rodamiento es importante

colocarlo utilizando una pistola de calor o una secadora de pelo, para así evitar dañar la pieza

al realizar fuerza.

Figura 34. Segundo paso del ensamblaje de la base.

Fuente: Elaboración propia.

El siguiente paso es colocar la pieza que conecta al rodamiento y en la cual se colocan

dos ventiladores para así ventilar los motores pasos a pasos con reduccion planetaria debido a

que estos tienden a sufrir un sobrecalentamiento, esta parte del ensamblaje se observa en la

siguiente Figura.

Figura 35. Tercer paso del ensamblaje de la base.

Fuente: Elaboración propia.

Paso 5: Instalación del Firmware

Para la instalación del firmware en el tablero de control, se usa el IDE de Arduino. (https://www.arduino.cc/en/software)

Una vez que se haya instalado, ir a la página de “Descargas” y descargue los archivos de

firmware más recientes.

Descomprimir | el | archivo | descargado | y | navegar | hasta | grbl-

1.0/grbl/examples/grblUpload. En esta carpeta hay un archivo llamado grblUpload.ino que se

debe abrir usando Arduino IDE.

Haga clic en Sketch > Incluir biblioteca > Agregar biblioteca .ZIP. En la nueva

ventana, navegue hasta la carpeta grbl-1.0/grbl y presione "Abrir" para incluirla en el proyecto

(no incluya el archivo .zip ni la carpeta grbl-1.0).

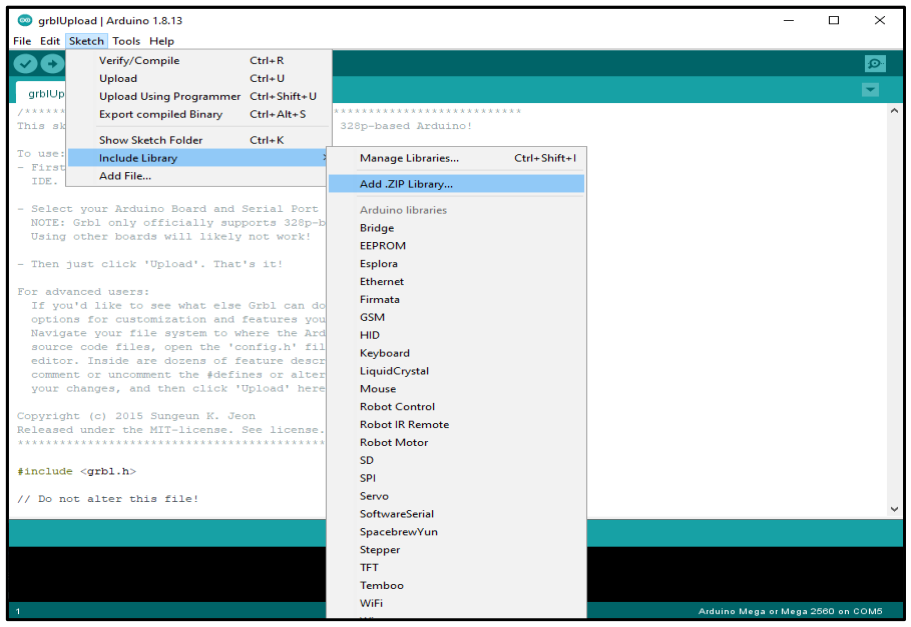
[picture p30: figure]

Figura 36. Primer paso de la instalación de GRBL.

Fuente: Elaboración propia.

Conectar el Arduino Mega a la PC sin tener la placa PCB conectada al Arduino.

En el IDE de Arduino, ir a Herramientas > Placa y seleccionar "Arduino Mega". Si no se

selecciona automáticamente, ir a Herramientas > Puerto y seleccionar el puerto donde está

conectada la placa como se observa en la siguiente Figura.

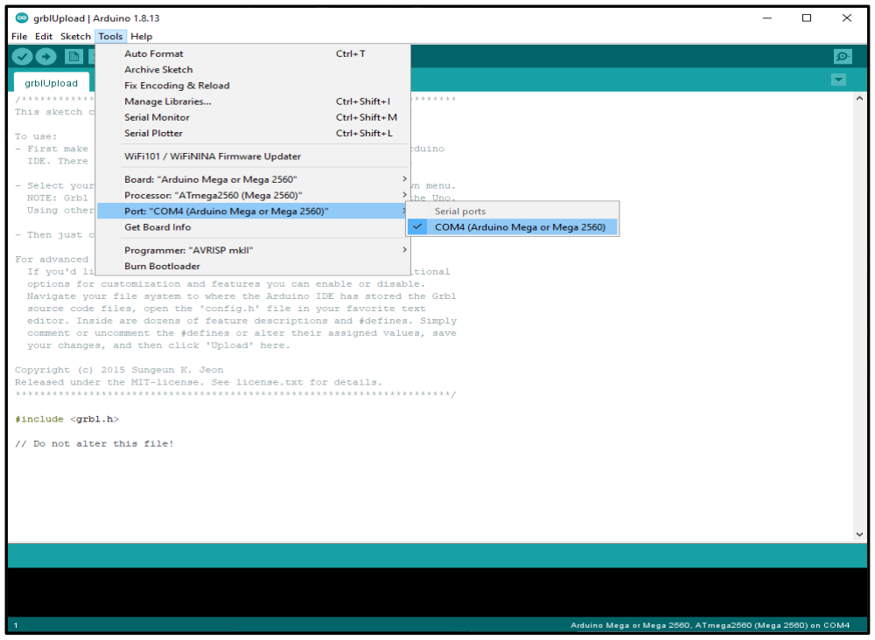
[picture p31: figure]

Figura 37. Segundo paso de la instalación de GRBL.

Fuente: Elaboración propia.

Presionar el botón Cargar (el que tiene una flecha horizontal) ubicado en la barra

superior. Después de unos segundos la carga finalizará y en la barra inferior debería aparecer

el siguiente mensaje: “Listo para cargar”.

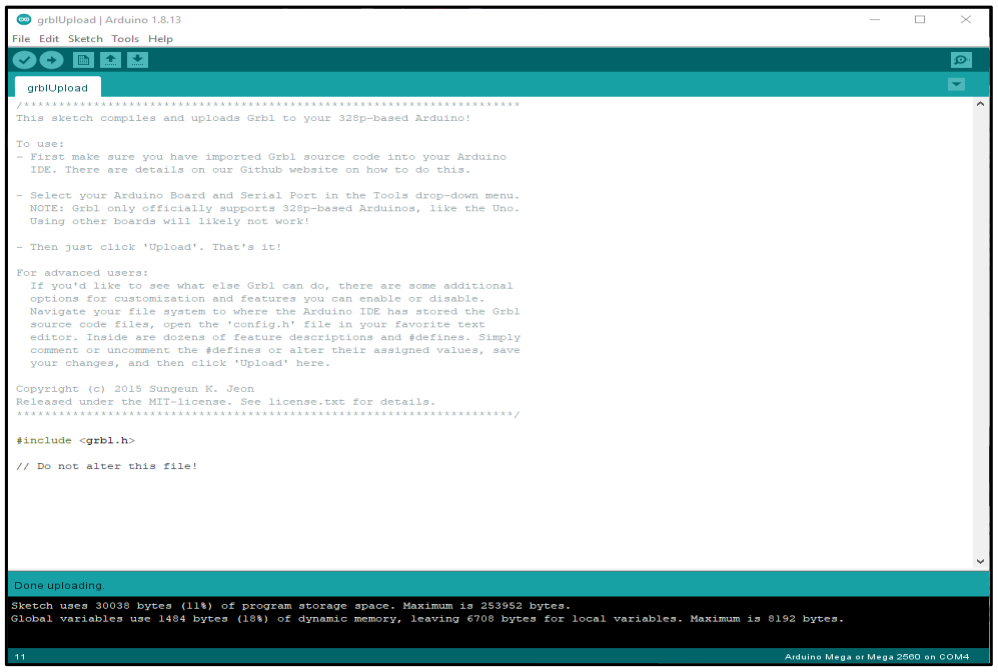
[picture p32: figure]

Figura 38. Tercer paso de la instalación de GRBL.

Fuente: Elaboración propia.

Una vez se realizan estos pasos se puede conectar la placa PCB al Arduino. y comenzar

con la configuración y pruebas.

Paso 6. Configuración de firmware

GBRL tiene una lista de ajustes (https://github.com/gnea/grbl/wiki/Grbl-v1.1-Configuration#---view-grbl-settings) que se pueden configurar. Para que funcione para

Thor, es necesario realizar algunos cambios.

Para realizar esta configuración puede utilizar la consola. En esta guía se usa el

integrado en el IDE de Arduino a pesar de que también el software Asgard lo tiene incorporado.

Con el Arduino conectado a la PC, abrir el IDE de Arduino y hacer clic en el botón

Serial Monitor (en el lado derecho de la barra superior). Debería aparecer una nueva ventana.

Hacer clic en el cuadro de selección de velocidad en baudios y seleccionar la opción

115200 si aún no está seleccionada y seleccione la opción "Nueva línea" en el otro cuadro de

selección. Ahora se debe ver el siguiente mensaje en la consola: “Grbl 0.9j ['$' para ayuda] –

Thor Versión 1.0”

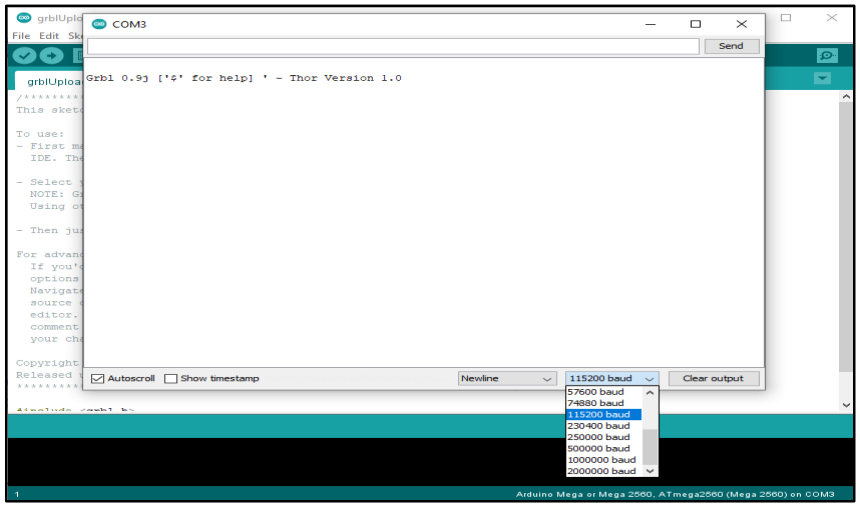
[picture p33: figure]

Figura 39. Cuarto paso de la instalación de GRBL.

Fuente: Elaboración propia.

Si se envía el comando $$ en el cuadro de texto de entrada y se presiona Intro, la placa

devolverá la configuración GRBL actual.

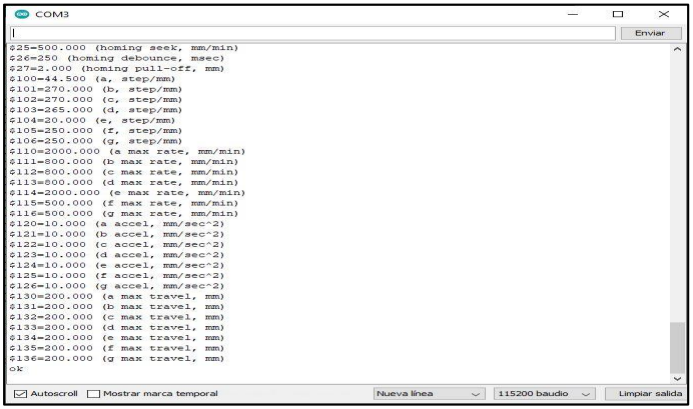
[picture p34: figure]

Figura 40. Quinto paso de la instalación de GRBL.

Fuente: Elaboración propia.

Por defecto, los parámetros deben coincidir con los mostrados previamente, pero estos

serán modificados en la integración del robot móvil.

En caso de que no coincidan, se puede intentar enviar el comando $RST=$. Este

comando reemplaza los valores de los parámetros con los predeterminados (es útil si se está

probando nuevos parámetros y se desea volver a los predeterminados).

También se puede cambiar los valores uno por uno enviando el comando donde

“parámetro” es el número del parámetro y “valor” es el valor del parámetro. Por ejemplo, para

configurar | el | tiempo | del | pulso | de | paso | en | 10 | usecs | se | envía | el

comando: $parameter=value$0=10

Figura 41. Último paso de la instalación de GRBL.

Fuente: Elaboración propia.

Prueba de firmware

Se usa GRBL para controlar los motores Thor. GBRL procesar los comandos de

GCode, por lo que sería una buena idea saber qué son los comandos de GCode. (https://reprap.org/wiki/G-code)

Estos serían los comandos básicos y cómo usarlos:

Mover: G0 y G1

Uso

G0 Annn Bnnn Cnnn Dnnn Xnnn Ynnn Znnn Fnnn G1 Annn Bnnn Cnnn Dnnn Xnnn

Ynnn Znnn Fnnn

Variables

No es necesario utilizar todas las variables, pero sí al menos una.

Annn: El ángulo al que girar en la primera articulación (motor n.º 1)

Bnnn: El ángulo al que girar en la segunda articulación (motor n.º 2)

CNN: El ángulo al que girar en la segunda articulación (motor n.º 3)

Dnnn: El ángulo al que rotar en la tercera articulación (motor n.° 4)

Xnnn: El ángulo al que girar en la cuarta articulación (motor n.º 5)

Ynnn: El ángulo al que girar en la quinta y sexta articulación (motor n.° 6)

Znnn: El ángulo al que girar en la quinta y sexta articulación (motor n.º 7)

Fnnn: La velocidad de avance por minuto del movimiento entre el ángulo inicial y el

ángulo final (si se proporciona)

Nota: B&C debe ser el mismo número

Ejemplos:

G0 A10 B45 C45 D-45 X15 Y5 Z-5Este código pasará al 10º el Art. 1º, al 45º el Art.

2º, al -45º el Art. 3º, al 15º el Art. 4º. y rotará la muñeca (Arte 5 y 6)

G1 A20 X-20 F1000Este código pasará al 20º del art. y a -20º el 4º Art a 1000

grados/min de velocidad

Herramienta: M3

Uso

M3 Snnn

Variables

Snnn: valor de señal de herramienta de salida

Ejemplos:

M3 S900 Este comando moverá un servomotor conectado al pin TABURETE de

ControlPCB a la posición abierta.

Esta guía es la guía proporcionada por Ángel que fue ligeramente modificada con unos

comentarios extras o consejos.

Paso 7. Software de control

Controlar una máquina enviando comandos GCode a través de la consola no es lo más

intuitivo.

Por eso existen interfaces gráficas como Universal GCode Sender (https://winder.github.io/ugs_website/) que facilitan esta

tarea. Desafortunadamente, como UGS fue diseñado para controlar máquinas CNC, no admite

el control de más de 3 motores paso a paso. Sobre la base de esta idea se desarrolló Asgard.

Asgard es una interfaz gráfica de usuario (GUI) creada para Thor, programada en

Python utilizando las bibliotecas PyQt5.

Instalación asgard

Como es un programa Python, no importa qué sistema operativo uses, todo lo que tienes

que hacer es instalar Python 3 y ejecutar Asgard. Para hacerlo, siga las instrucciones a

continuación:

− Vaya al sitio de descargas de Python (https://www.python.org/downloads/) , descargue la última versión de Python 3 e instálela

en su PC.

− Vaya a la sección Descargas (http://thor.angel-lm.com/downloads/) de este sitio, descargue el código fuente de Asgard y

descomprima el archivo en una ubicación conocida.

− El siguiente paso es asegurar que se tiene instalado las bibliotecas PyQt5, la cual se

puede instalar directamente desde la terminal del sistema con el siguiente código:

pip install PyQt5

− Abrir la terminal de su sistema, instalar PyQt5 y navegar hasta la carpeta de archivos de

Asgard para así ejecutar la interfaz.

− Una vez que esté en la misma carpeta que el archivo 'asgard.py', ejecute el

comandopython asgard.py

Es probable que el paso anterior arroje errores de dependencia que debas resolver para

poder ejecutar Asgard. Para resolverlos tendrás que instalar algunas librerías, para hacerlo

simplemente ejecuta este comando si es que el código recomendado previamente no funciona:

python -m pip install pyqt5 pyserial numpy pyqtgraph pyopengl.

Una vez finalizada la instalación de las bibliotecas, se debe reiniciar la computadora

para así ejecutar el comando python asgard.py nuevamente sin ningún error.

Uso de Asgard

Aunque el programa es bastante fácil de utilizar, no está de más explicar cada una de

sus características. Conexión de la placa:

Figura 42. Conexión de la placa mediante Asgard.

Fuente: Elaboración propia.

Puerto serie: cuadro combinado para seleccionar el puerto al que está conectada la

placa. El botón del lateral se utiliza para actualizar la lista de puertos.

Velocidad de baudios: velocidad de comunicación, 115200 baudios por defecto.

Estado: Display que muestra el estado actual de la placa (Desconectado, Inactivo, En

ejecución o Alarma).

Botón Conectar: Una vez seleccionado el puerto serie, haga clic en él para establecer

la conexión. Controles generales:

Figura 43. Botones extra en Asgard.

Fuente: Elaboración propia.

Botón de inicio: ejecuta el comando de inicio ($H).

Posición cero: Ejecuta el comando para mover el robot a la posición cero (G0 A0 B0

C0 D0 X0 Y0 Z0)

Kill Alarm Lock: cuando falla el ciclo de inicio, se activa el modo de alarma y se

bloquean los movimientos del robot. Este botón ejecuta el comando para cancelar el bloqueo

de alarma ($X).

Modo de movimiento G0/G01: Cambia entre G0 (movimiento rápido) y G1

(movimiento de velocidad controlada).

Velocidad de alimentación: entrada de velocidad de movimiento. Habilitado cuando

se selecciona G01 Mover.

Cinemática directa

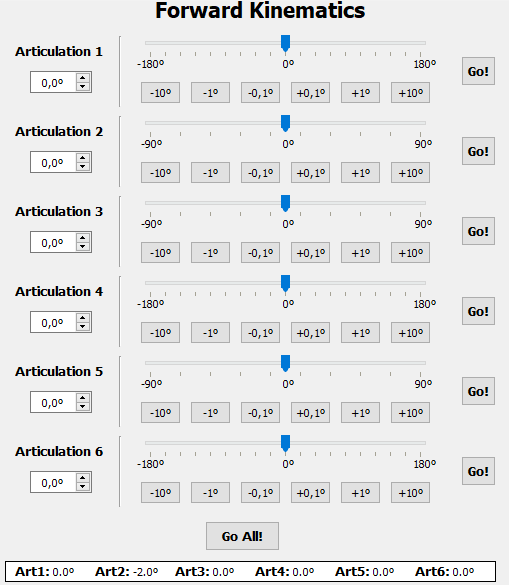
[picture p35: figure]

Figura 44. Cinemática Directa en Asgard.

Fuente: Elaboración propia.

Cada articulación tiene tres formas diferentes de introducir el ángulo objetivo (cuadro

de entrada, control deslizante y botones) y un botón “Ejecutar” Botón para mover la

articulación.

“Ejecutar todo” Es un botón que en lugar de mover cada articulación individualmente,

este botón envía el comando de movimiento para mover todas las articulaciones a la vez.

Pantalla de ángulos: esta pantalla muestra los ángulos de articulación actuales del

robot.

Control de pinza

Figura 45. Control de la garra en Asgard.

Fuente: Elaboración propia.

De manera similar al control Articulaciones FK, hay tres formas de ingresar la señal que

controla la herramienta del robot y un mensaje “Ejecutar” Botón para enviar el comando.

Consola

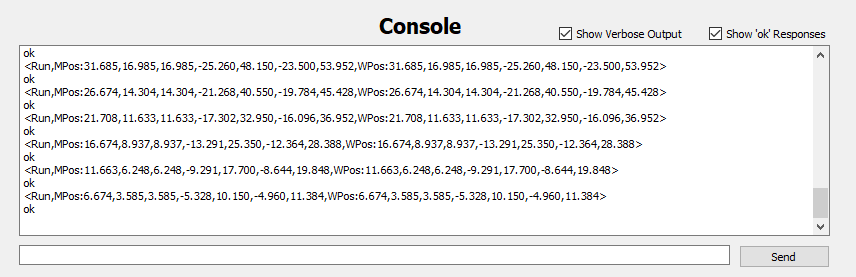
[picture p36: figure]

Figura 46. Consola de Asgard.

Fuente: Elaboración propia.

En la parte inferior hay una consola serie, similar a la de Arduino, que muestra cada

comando enviado hacia/desde la placa. También hay un cuadro de texto donde se pueden

escribir comandos y un botón " Enviar " para enviarlo al tablero.

Mostrar salida detallada: esta casilla de verificación le permite mostrar/ocultar los

mensajes detallados enviados por el tablero que contienen la información de estado y posición.

Mostrar respuestas 'ok': esta casilla de verificación le permite mostrar/ocultar las

respuestas 'ok' enviadas por el foro.

Como se puede observar, esta guía también se puede leer en la página de Thor, la cual

fue ligeramente modificada con algunos consejos propios.

Una vez se comprueba el funcionamiento de Asgard, sin realizar ningún cambio en el

código, se proceden a realizar los cambios para la integración del robot móvil.

El primer paso es determinar donde se encuentran los pines a modificar dentro de la

librería de grbl, ya que esta determina el movimiento de los motores paso a paso. Las cuales las

librerías que se modifican son las siguientes: stepper.c, limits.c , limits.h, stepper.h y la librería

cpu_map_atmega2560.h.

Dentro de estas librerías se declaran los puertos y los pines donde se encuentran cada

uno de los motores, el cual funciona mediante el uso de bits del Arduino Mega, las nuevas

conexiones se realizaron con guía de esta imagen para así saber el valor en bits de cada pin.

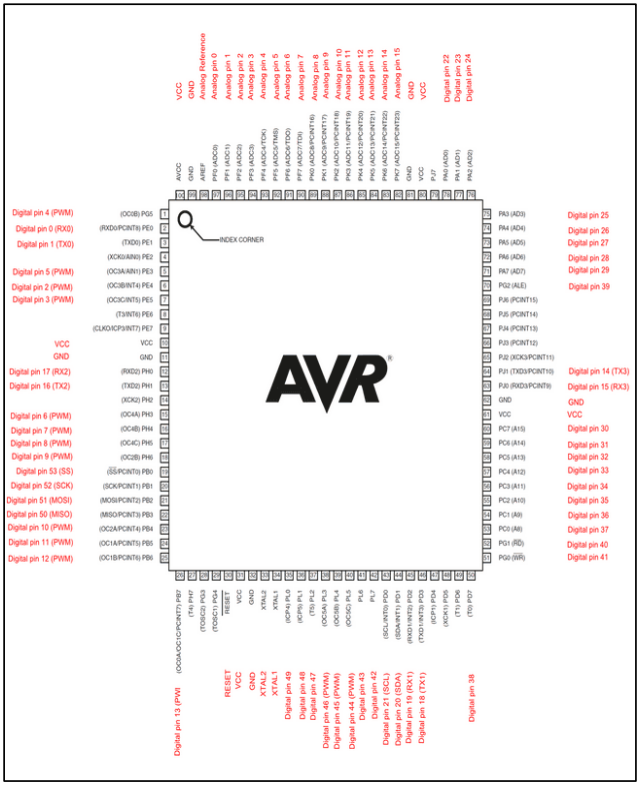
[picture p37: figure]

Figura 47. Esquema de pines en el Arduino Mega.

Fuente: Elaboración propia.

Como se aprecia en la figura anterior, el pin 30 se caracteriza por tener un bit 7, lo cual

se refleja en su denominación "PC7". Para cada motor que se desee utilizar, es necesario

modificar el código correspondiente. Esto implica la definición del pin de dirección, el puerto

al que está conectado, el pin asignado a ese puerto y, por último, el bit que se asigna a dicho

motor. Este proceso se repite para cada motor que se incorpore al sistema, como se muestra en

la siguiente figura.

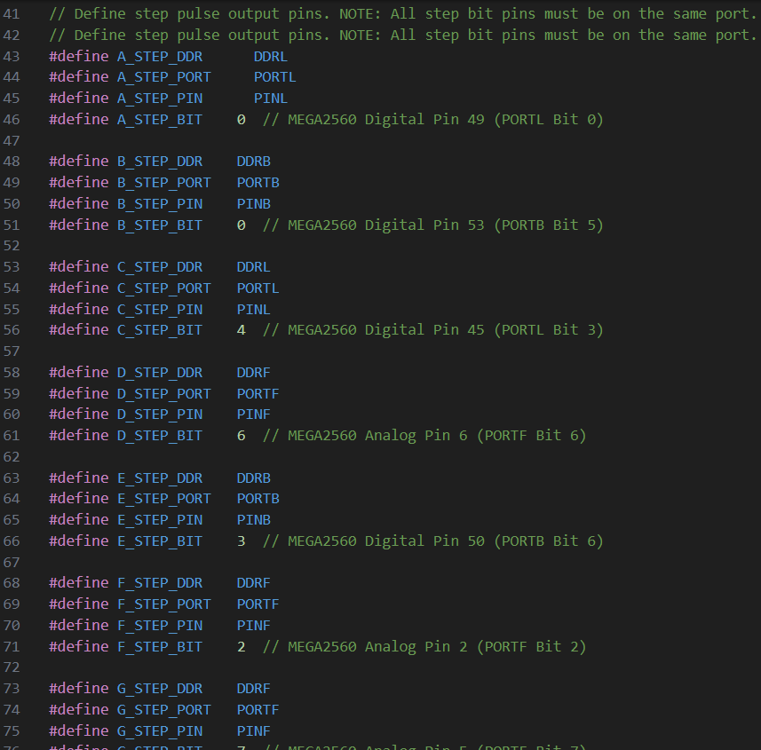
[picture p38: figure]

Figura 48. Modificación de código Asgard.

Fuente: Elaboración propia.

Una vez se realiza este paso, es recomendable tratar de correr el código de la librería

grbl, ya que aún faltan bastantes variables para cambiar de nombre, pero el Arduino facilita el

trabajo para saber en qué línea exactamente realizar este cambio y así no perder tiempo

buscando línea por línea.

Una vez se realizan estos cambios, se procede a realizar el ensamblaje del robot móvil,

el cual se empieza por las ruedas, el primer paso es colocar el rodamiento a cada una de las

tapas de las ruedas para así amortiguar el movimiento que realiza el eje, como se muestra en la

siguiente Figura.

Figura 49. Primer paso en el ensamblaje de la rueda.

Fuente: Elaboración propia.

El siguiente paso es colocar la polea que se acopla a una de las tapas de las ruedas y

también se colocan las varillas que atraviesan de lado a lado en cada rueda para que así al

momento de colocar los rodillos no se despegue la pieza.

Figura 50. Segundo paso en el ensamblaje de la rueda.

Fuente: Elaboración propia.

Por último, se debe colocar las arandelas correspondientes a cada uno de los rodillos

para que así el movimiento que realiza cada uno de los rodillos no desgaste la pieza mediante

la varilla que atraviesa el rodillo, como se observa en la siguiente Figura se van colocando los

rodillos poco a poco.

Figura 51. Último paso en el ensamblaje de la rueda.

Fuente: Elaboración propia.

Finalmente, se debe realizar la construcción de la plataforma móvil, la cual se puede

observar en el documento las medidas de la plataforma móvil, el trabajo para la construcción

de la plataforma móvil si es que se utiliza los mismos materiales, se requiere un espacio de

trabajo al aire libre y que cuenten con las herramientas necesarias para realizar cortes, como ser

una amoladora para los cortes de los tubos de metal con las medidas exactas que se requieren y

sierra para madera para así cortar la tabla que se coloca encima de los tubos. Finalmente, se

deben colocar tornillos alrededor para así asegurar la conexión y estabilidad. Como se puede

observar a continuacion se ve el robot móvil solamente con dos de las cuatro ruedas

omnidireccionales.

Figura 52. Primer paso del ensamblaje de la plataforma móvil.

Fuente: Elaboración propia

En la siguiente Figura se colocan las otras dos ruedas omnidireccionales, se debe tener

especial cuidado en el orden de las ruedas, debido a que si no se las coloca en la manera en que

deben ir, las ruedas no realizarán los movimientos de manera omnidireccional. Se debe que la

rueda delantera de la izquierda coincide con la orientacion de los rodillos de la rueda trasera de

la derecha y asímismo con las otras ruedas. Posterior a ello, se realiza un analisis de este recurso

educativo digital.

Figura 53. Último paso del ensamblaje de la plataforma móvil.

Fuente: Elaboración propia

ANÁLISIS DEL RECURSO EDUCATIVO DIGITAL

Para realizar el análisis se debe tener conocimiento de los desafíos que se presentaron

en la elaboración del proyecto y las soluciones que se dan para estos desafíos como se observa

en la siguiente Tabla.

Tabla 5. Desafíos y soluciones del proyecto.

Desafíos en la Integración
de Robots | Descripción | Soluciones

Escasez de materiales clave

Dificultades en la adquisición de correas, motores paso a paso, poleas, fuentes de energía de alto amperaje, pernos, tuercas y arandelas específicas.

Investigación exhaustiva de alternativas, búsqueda de sustitutos viables, adaptación del diseño para materiales disponibles.

Limitaciones en la fabricación de componentes

Problemas con el diseño de la PCB como la falta de librerías de ciertos componentes, soldadura y adaptación del diseño a recursos limitados.

Ajustes en el diseño, soluciones técnicas específicas para la fabricación de la PCB y soldaduras de doble cara.

Proceso de ensamblaje afectado | Escasez de elementos de sujeción, complicaciones en el montaje.

Uso de métodos alternativos de ensamblaje, adaptaciones manuales para solucionar la falta de elementos.

Restricciones en la impresión de CAD

Limitaciones en la impresión de diseños CAD debido a componentes específicos.

Adaptación de diseños para optimizar la fabricación con los recursos disponibles.

Fuente: Elaboración propia.

Una vez se tiene estos desafíos y soluciones se debe realizar un análisis a detalle de

estos, en el cual se observan también las habilidades adquiridas y como mediante estas

soluciones se logra cumplir los objetivos establecidos en el proyecto.

Habilidades Adquiridas y Mejoradas

Durante la elaboración del proyecto de grado, cuyo objetivo principal es desarrollar un

aporte educativo de código abierto mediante la integración de un robot móvil y un brazo

robótico de 6 grados de libertad para promover la enseñanza y ampliar los recursos educativos

de robótica en Bolivia, se adquieren y mejoran una serie de habilidades fundamentales. Estas

habilidades no solo se relacionan con la tecnología y la robótica, sino también con la

planificación y la resolución de problemas.

A continuación, se destaca algunas de las habilidades más relevantes que se adquieren

y se pueden perfeccionar a lo largo de este proceso:

- Conocimiento Técnico: Durante la investigación y desarrollo del proyecto, se

adquieren bastantes conocimientos técnicos en robótica, programación,

electrónica y mecánica. Se aprende a trabajar con sistemas de control, sensores,

actuadores y algoritmos de planificación de movimientos.

En el ámbito de la robótica existen diferentes campos como ser la mecánica, la

eléctrica y de software. En el proceso se adquieren conocimientos sobre como

calcular la cinemática directa e inversa tanto del robot manipulador como móvil,

en el cual se observa que la manera en que se obtienen las cinematica de cada

uno de los robots y los datos que se consideran tiene gran diferencia una con la

otra para realizarla, estos conceptos son fundamentales en la robótica y requieren

un entendimiento de matemáticas, particularmente el álgebra lineal.

Además de estos aspectos matemáticos, también es importante familiarizarse

con la terminología específica de la robótica, que incluye conceptos como

cinemática, trayectorias, articulaciones, coordenadas, singularidades, entre

otros.

Al abordar estos conceptos se promueve la enseñanza de la robótica y ofrece a

los estudiantes la oportunidad de explorar y aplicar estos conocimientos en un

proyecto práctico.

- Programación y Desarrollo de Software: Mejoran las habilidades de

programación al modificar y adicionar en el software que controla tanto el robot

móvil como el brazo robótico. Se utilizan lenguajes como Arduino y Python para

programar y controlar los componentes del proyecto.

El aprendizaje y la mejora de las habilidades de programación son

fundamentales especialmente en Arduino porque es una plataforma ampliamente

conocida y utilizada en la comunidad de entusiastas de la robótica. En este

proyecto se mejoran las habilidades de programación en Arduino. La inclusión

de librerías simplifican el uso de los motores paso a paso especialmente la

librería de GRBL, el cual se utiliza para el control preciso de motores paso a

paso, además de que es importante la capacidad de integrar Arduino y Python es

importante ya que permite la creación de interfaces que permiten un mayor

control y monitoreo del robot manipulador móvil.

El objetivo de la integración de Arduino y Python es crear una interfaz amigable

que hace que sea más fácil para los estudiantes interactuar con los robots y

comprender cómo funcionan. Además de que es importante entender al menos

lo básico debido a que es posible que no se utilicen los mismos pines, por lo

tanto, se los deben modificar y para ello se debe entender lo básico tanto de

Python como de Arduino.

- Diseño Mecánico y Electrónico: Se aprende a diseñar y construir componentes

mecánicos y electrónicos para el robot móvil y el brazo robótico. Esto incluye el

diseño de placas de circuito impreso, selección de motores y componentes

mecánicos, así como la integración de sensores.

En este ámbito se permite aplicar conceptos teóricos en situaciones prácticas,

esto refuerza su comprensión de los conceptos teóricos. Para el diseño

electrónico se debe tener un procedimiento a tomar en cuenta, el primer paso es

el de conocer los componentes electrónicos que se utilizan, es decir, cuantos

actuadores, cuantos sensores, cual es el controlador del sistema. Posterior a ello,

se debe revisar la hoja de datos de cada componente, principalmente para

conocer el voltaje que soporta cada componente y ejemplos de cómo realizar las

conexiones. Por ejemplo, existe un voltaje máximo diferente entre el Arduino

Mega y los motores paso a paso, el Arduino Mega soporta 5V y los motores paso

a paso soportan 12V, además de que también los finales de carreras y

ventiladores a utilizar tienen diferente voltaje, por lo tanto, con el conocimiento

previo de esto, se determina que se necesita un regulador de voltaje para la placa

electrónica. Al realizar diseños electrónicos se aprende habilidades técnicas del

uso de programas de diseño de circuitos como ser Proteus y KiCAD que

permiten el diseño de PCB’s, también se aprenden habilidades de soldadura una

vez se procede a realizar la placa en físico.

En el diseño mecánico se aprende principalmente a analizar primero la selección

del material adecuado para esta aplicación en específico considerando la

durabilidad y el costo del material. Posterior a la selección de material es

importante adquirir habilidades en diseño y modelado utilizando software CAD

para su posterior prototipado. Luego a la selección de material se aprende a que

se deben realizar análisis de esfuerzos para así evaluar cómo la estructura resiste

las cargas y las tensiones a las que se le somete. Además de que se adquieren conocimientos sobre el prototipado rápido mediante la impresión 3D, debido a

que principalmente se debe conocer cómo manipular una impresora 3D y cómo

realizar la configuración para la impresión, debido a que se deben tomar distintas

variables para la misma, ya que mejoran o afectan al procedimiento según la

pieza a imprimir.

- Investigación y Análisis: La fase de investigación requerida para este proyecto

permite mejorar las habilidades de investigación y análisis, como también la

capacidad de identificar y evaluar fuentes de información pertinentes y analizar

datos experimentales para tomar decisiones fundamentadas.

La investigación tiene distintas fases dentro de la misma, debido a que antes de

comenzar la investigación, es importante definir con claridad el objetivo o los

objetivos que se pretenden alcanzar. En este caso luego de definir estos

objetivos, se mejoran las habilidades para identificar y evaluar las fuentes de

información.

Mediante la revisión de la literatura se mejoran las habilidades de investigación

ya que se revisa literatura existente relacionada al tema de interés. Al analizar

documentos académicos, libros, informes y sitios web se comprende el estado

actual del tema de interés.

- Resolución de Problemas: Durante la construcción y puesta en marcha del

robot, se enfrenta a numerosos desafíos técnicos y desarrolla la habilidad de

identificar problemas, proponer soluciones y realizar pruebas para verificar la

eficacia de las soluciones.

En este punto se relacionan diferentes habilidades anteriormente mencionadas,

debido a que para la resolución de problemas, se debe utilizar la habilidad de

investigación para investigar problemas similares que han ocurrido en el pasado,

por ejemplo, en el proyecto se presentó distintas dificultades en el manejo de los

motores paso a paso como ser la correcta distribución de corriente a cada uno de

los motores, ya que si circula menos corriente de la necesaria, el motor no realiza

sus movimientos correctamente, pero si envía mayor corriente pasa lo mismo y

existe riesgo de arruinar el motor, por lo tanto, se debe realizar una profunda

investigación sobre los problemas que ocurren comúnmente con los motores

paso a paso.

También existen distintos problemas en el ensamblaje, por lo tanto, es

importante desarrollar la habilidad de identificar en qué parte está el problema y

proponer una solución. En el presente proyecto existe un problema, el cual va

relacionado a los engranajes del articulación 4 y 5, debido a que las poleas que

se venden en las electrónicas locales, tienen distintas medidas a las que presenta

el autor del robot manipulador, por lo tanto, la primer solución fue rellenar el

espacio sobrante con un pedazo de correa, para así poder encajar la polea en el

engranaje impreso, lo cual fue una solución temporal para luego realizar su

posterior rediseño de la pieza.

También existieron distintos problemas debido a la disponibilidad de

componentes y materiales necesarios para el proyecto, en el que debido a que no

existía stock de lo solicitado, se debió realizar distintas modificaciones como ser

los rodamientos y la varilla que funciona como eje en el robot móvil.

- Gestión de Proyectos: Planificar y llevar a cabo un proyecto de esta magnitud

enseña valiosas lecciones sobre la gestión de proyectos. Se aprende a establecer

metas, plazos y recursos, y a hacer un seguimiento constante del progreso.

Esta habilidad es importante debido a que una correcta gestión del proyecto

marca fechas de inicio y finalización de las diferentes tareas y etapas del

proyecto. Además de que dentro de este tiempo se deben considerar los posibles

riesgos que podrían afectar al calendario del proyecto, por lo tanto, se debe

establecer un tiempo mínimo de correcciones para así evitar retrasos no

planificados en el proyecto.

- Conciencia Social y Educativa: Este proyecto es para sensibilizar sobre la

importancia de la educación en robótica en Bolivia y la necesidad de tener

recursos educativos accesibles y desarrollar conciencia social y de compromiso

con la mejora de la educación en el país.

Este proyecto presenta distintas dificultades debido al poco desarrollo de la

robótica en Bolivia, lo cual genera preocupación en general, debido a que se

tuvieron que realizar distintas consideraciones y modificaciones, ya que a la hora

del prototipado en la búsqueda de los componentes, se encuentra que existe poco

material para el desarrollo de proyectos sobre robótica .

CUADRO COMPARATIVO DE CALIFICACIÓN

Tabla 6. Desafíos y soluciones del proyecto.

Habilidad | Antes del Proyecto Después del Proyecto
Conocimiento Técnico General | Principiante | Intermedio
Programación y Desarrollo de Software | Principiante | Intermedio
Diseño Mecánico y Electrónico | Principiante | Intermedio-Avanzado
Investigación y Análisis | Principiante | Avanzado
Resolución de Problemas | Principiante | Intermedio
Gestión de Proyectos | Principiante | Intermedio
Conciencia Social y Educativa | Baja | Media

Fuente: Elaboración propia

EVALUACIÓN DE LOS OBJETIVOS

Se lleva a cabo la evaluación de los objetivos específicos y se demuestra que fueron

logrados de manera efectiva los mismos, en el desarrollo del proyecto de integración de un

robot móvil y un brazo robótico con el propósito de promover la enseñanza y ampliar los

recursos educativos de robótica en Bolivia, se proporcionará ejemplos de las evidencias

concretas para cada uno de los objetivos específicos que respaldan el trabajo:

- Definir los requisitos funcionales del robot móvil y brazo robótico

incluyendo capacidad de carga, velocidad máxima, autonomía, dimensiones

físicas, costos y disponibilidad de componentes en el mercado local.

Se establecen los requisitos funcionales en el documento en el capítulo 3.

Se establece para el robot móvil una capacidad de carga máxima de 80 kg, lo que permite

que el robot móvil soporte el peso del brazo manipulador y los componentes extras que se

colocan, como ser la batería y la caja de componentes electrónicos. El cual se demuestra

mediante el cálculo realizado donde se establece cuánto peso soporta la plataforma móvil.

El brazo manipulador debe ser capaz de manipular objetos de hasta 750 gramos.

Se define la autonomía mínima de 1 hora para el robot manipulador móvil, lo que

garantiza un funcionamiento eficiente. Esta autonomía se logra a través de de una batería de

12V 40A, la cual se realiza el cálculo en el capítulo 4 y se demuestra cuánto es la duración de

la batería.

Las dimensiones físicas del robot móvil se ajustan al espacio de trabajo del robot

manipulador, además de que se considera un espacio extra para los componentes extras.

Se establece un presupuesto máximo en los capítulos 3 y 4, en el cual se especifica el

presupuesto máximo para cada uno de los robots. Este presupuesto incluye el costo de los

materiales, sensores, actuadores y otros componentes necesarios para la construcción del

sistema robótico.

Se realiza una investigación presente en el documento respecto a los proveedores

confiables que existen en el mercado local, en el cual los componentes utilizados en el proyecto

son obtenidos de las tiendas “Sawers”, “Ardunel”, “EPYElectronics”, “EcRobotics”. Además

de que mediante estas se consulta la disponibilidad de los componentes utilizados en el

proyecto.

- Seleccionar un brazo robótico de código abierto

Se presenta una justificación de la elección del brazo robótico, destacando cómo se

cumplieron los factores de selección, como especificaciones técnicas, configuración del robot,

rango de movimiento, flexibilidad, documentación y comunidad de usuarios en el capítulo 3.

Se realizan adaptaciones al brazo manipulador seleccionado, y se documenta el porqué

fueron necesarias en el capítulo 3.

- Desarrollar un robot móvil

En el capítulo 4 del documento se presenta el desarrollo de los modelos CAD del robot

móvil. Estos modelos permiten visualizar el diseño en su totalidad en el cual se visualizan las

dimensiones mostradas en los planos mostrados en los Anexos.

En el capítulo 4 se desarrolla la selección de materiales y componentes necesarios para

la elaboración del robot móvil en el cual se consideraron diferentes factores técnicos para

cumplir con los requisitos del proyecto.

En el documento se presenta la integración del robot móvil con el robot manipulador

mediante la placa electrónica, en el cual se toman en cuenta los componentes previamente

establecidos del brazo manipulador y se analizan los componentes que se incluyen en el robot

móvil.

- Establecer una interfaz intuitiva de código abierto

Documentación técnica que describe la interfaz de control de manera detallada,

incluyendo cómo los usuarios pueden controlar y la interaccion de los movimientos del robot

manipulador móvil. Este código incluye la implementancion de las cinematicas de cada uno de

los robots para su verificar su funcionamiento.

Código fuente de la interfaz de control disponible en un repositorio de código abierto.

- Documentar los recursos educativos

Manuales de ensamblaje detallados que guían a los usuarios en la construcción del robot

móvil y brazo robótico.

Se incluyen diagramas electrónicos y mecánicos que muestran la estructura y el

funcionamiento del robot. La disposicion y la interconexion entre los diferentes componentes

para observar su integración.

Disponibilidad de la documentación en el repositorio virtual educativo de acceso

público en el cual se observa también una presentación del material audiovisual que muestra el

proyecto en pleno funcionamiento, en el cual se demuestra la coordinación y ejecución de sus

movimientos establecidos.

Se adjuntan fotografías que documentan el proceso de construcción del proyecto, desde

la etapa inicial hasta la final.

- Simulaciones y experimentos

Se realizan a cabo pruebas exhaustivas para verificar la precisión de los movimientos,

la comunicación entre los robots y la capacidad de trabajar en conjunto. Se realizan ajustes y

refinamientos en el software y en la mecánica para mejorar la eficiencia y la precisión del

sistema.

La comunicación entre los robots se lleva a cabo sin problemas, permitiendo una

coordinación eficaz en la realización de tareas conjuntas, demostrando la capacidad de

interacción y colaboración entre ambos dispositivos.

EVALUACIÓN DE IMPACTO

A. Ventajas Educativas

Las ventajas educativas del proyecto son significativas y pueden contribuir al avance de

la enseñanza y el aprendizaje de robótica en Bolivia de las siguientes maneras:

- Fomento de la enseñanza práctica: Los recursos desarrollados, incluyendo el robot

móvil y el brazo robótico, permiten a los estudiantes y entusiastas de la robótica tener

experiencias prácticas y aplicar conceptos teóricos en un entorno real. Esto fomenta un

aprendizaje activo y significativo. Además de que tiene un enfoque multidisciplinario

que permite a los estudiantes comprender conceptos de mecanica, electronica e

informatica.

- Acceso a tecnología de vanguardia: Al proporcionar acceso a tecnología de robótica

avanzada de código abierto, el proyecto permite a los estudiantes y educadores

familiarizarse con herramientas y conceptos de vanguardia, lo que puede ser

especialmente valioso en el mundo tecnológico actual. Además de que esta integración

brinda un antecedente sólido para proyectos de investigación similares a este.

- Fomento de habilidades técnicas: Los recursos del proyecto promueven el desarrollo

de habilidades técnicas en áreas como programación, electrónica, mecánica y control de

robots. Estas habilidades son altamente relevantes en la era digital y pueden mejorar la

empleabilidad de los estudiantes. Al realizar la integración el robot móvil amplia la

cobertura de área en comparación de solamente un brazo manipulador.

- Colaboración y aprendizaje colaborativo: Los recursos del proyecto pueden fomentar

la colaboración entre estudiantes, ya que pueden trabajar juntos en proyectos de

robótica, lo que refleja la forma en que se abordan los problemas en el mundo real.

B. Accesibilidad y Utilidad
- Facilidad de uso: Los recursos están diseñados con una interfaz intuitiva, lo que

facilita su uso tanto para principiantes como para usuarios más avanzados. Se

han proporcionado manuales y documentación detallada para guiar a los

usuarios.

- Información valiosa: La documentación incluye manuales de ensamblaje,

diagramas técnicos y recursos educativos que proporcionan información valiosa

sobre el funcionamiento y la construcción de los robots. Esto es esencial para

apoyar el aprendizaje y la comprensión de la robótica.

- Disponibilidad de código abierto: El proyecto ha adoptado un enfoque de

código abierto, lo que lo hace accesible para una amplia audiencia. Los recursos y la documentación están disponibles en línea, lo que facilita el acceso a

cualquier persona interesada en la robótica.

C. Impacto a Largo Plazo
- Influencia en futuros estudiantes y entusiastas de la robótica: El proyecto

puede servir como una fuente de inspiración para futuros estudiantes y

entusiastas de la robótica en Bolivia. Al proporcionar recursos y herramientas

educativas accesibles, se puede fomentar un interés duradero en la robótica.

- Mejora de la educación en robótica: A largo plazo, el proyecto tiene el

potencial de mejorar la calidad de la educación en robótica en Bolivia al

proporcionar recursos y tecnología de vanguardia a instituciones educativas y

estudiantes. Esto puede llevar a una fuerza laboral más capacitada en el campo

de la robótica en el país.

- Desarrollo de proyectos e innovación: Los recursos del proyecto pueden

inspirar a estudiantes y entusiastas a desarrollar proyectos innovadores en

robótica, lo que a su vez podría tener un impacto positivo en la industria y la

tecnología en Bolivia.
